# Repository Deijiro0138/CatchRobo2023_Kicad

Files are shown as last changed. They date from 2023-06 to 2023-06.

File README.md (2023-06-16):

# キャチロボ専用基板　仕様書
## マイコン
- Raspberry Pi Pico W x1

## 使用するアクチュエータ・センサ
- ステッピングモーター x2
- サーボ x3
- フォトリフレクタ x4
- 圧電スピーカー x1

## ピン配置
- GP0~2(サーボ)
- GP3(圧電スピーカー)
- GP6(モータ①Step),GP7(モータ①Dir)
- GP10(モータ②Step),GP11(モータ②Dir)
- GP12(遠隔非常停止)
- GP14(アナログマルチプレクサA),GP15(アナログマルチプレクサB)
- GP18~21(DIPスイッチ0-3)
- GP28(センサ読み取り用:ADC)

Raspberry Pi Picoのピン配置

### MD・ステッピングモーター
使用するMDは[STSPIN220](https://akizukidenshi.com/catalog/g/gK-14790/)であり,
**Dirピン→方向**
**Stepピン→回転**
を指定する.

[17HS16-2004S1データシート](https://www.omc-stepperonline.com/download/17HS16-2004S1.pdf) <br>
[Amazon上でのサイトページ](https://www.amazon.co.jp/Nema-%E3%82%B9%E3%83%86%E3%83%83%E3%83%94%E3%83%B3%E3%82%B0%E3%83%A2%E3%83%BC%E3%82%BF-%E3%83%90%E3%82%A4%E3%83%9D%E3%83%BC%E3%83%A91-8%C2%B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)

### アナログマルチプレクサ
アナログマルチプレクサはA,Bの2つの信号で読み取るチャンネルを切り替えられる.以下の真理値表を参照してほしい.
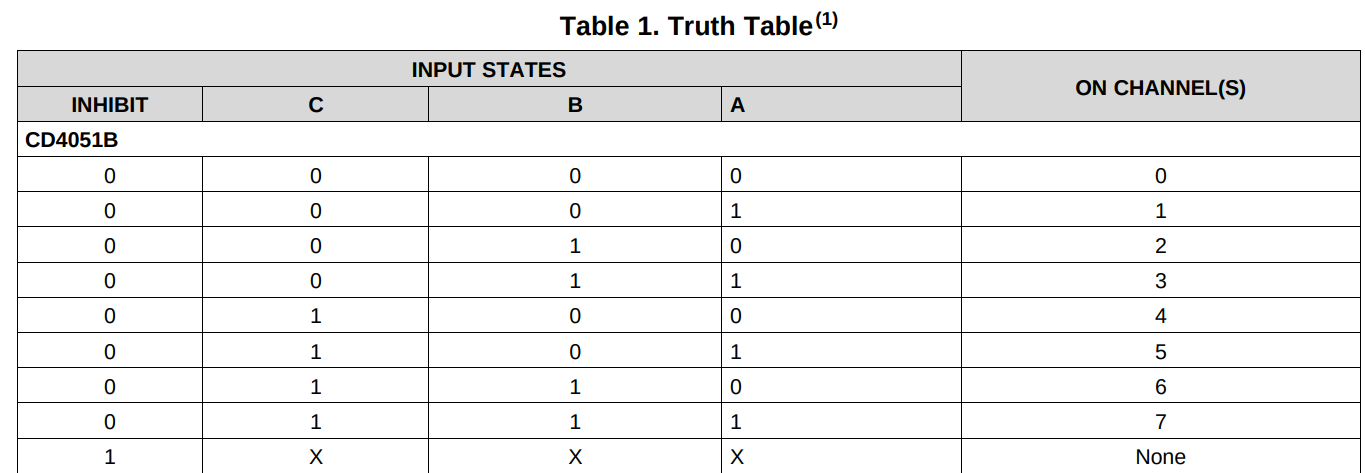
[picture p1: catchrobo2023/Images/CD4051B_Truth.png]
真理値表

AはGP15,BはGP15に接続されている.**GP28のADC機能を用いて,チャンネルを切り替えながら周囲の障害物を検知する.** <br>
[CD4051BM96データシート](https://datasheet.lcsc.com/lcsc/1809261612_Texas-Instruments-CD4051BM96_C21379.pdf)

## 回路図（暫定）
以下のファイルに現在の暫定版の回路図がある.
catchrobo2023/catchrobo2023.pdf
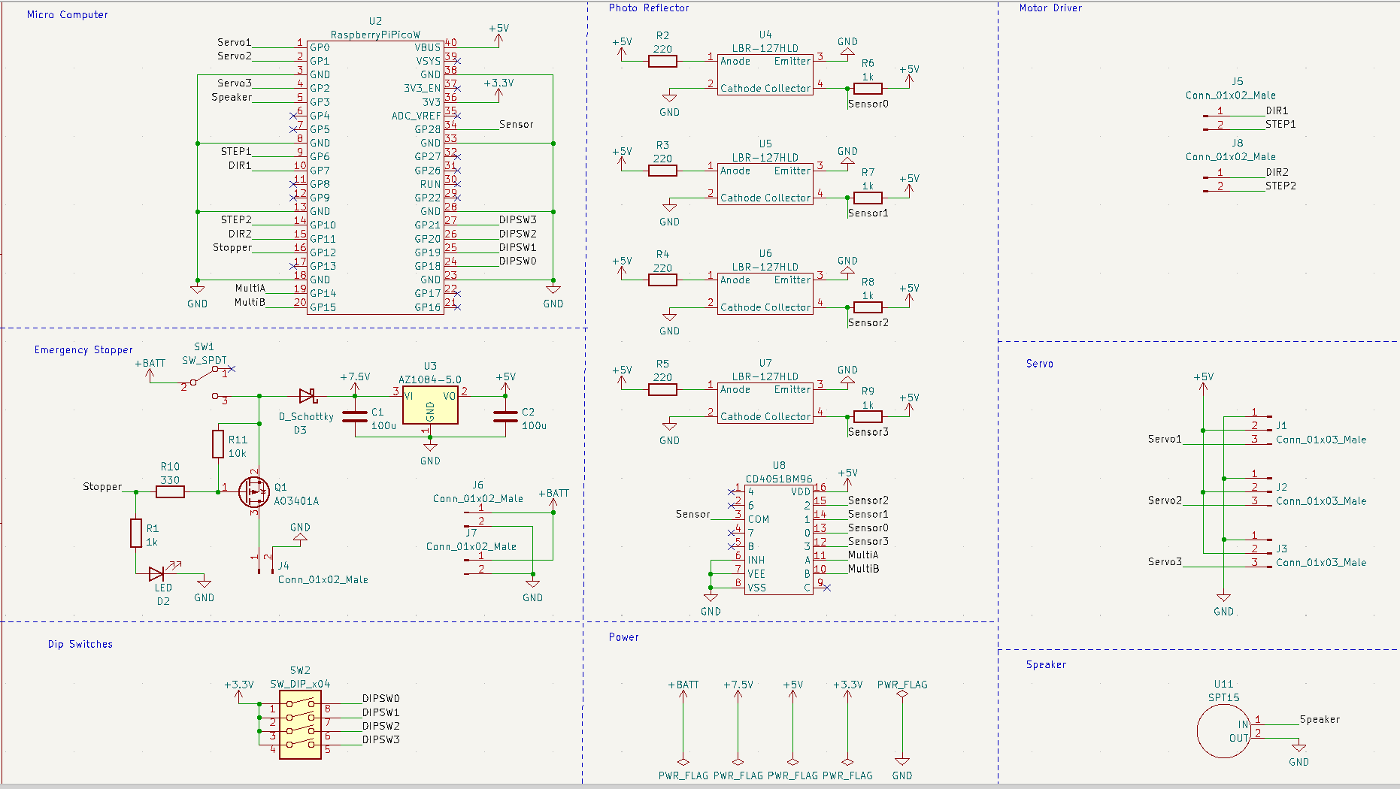
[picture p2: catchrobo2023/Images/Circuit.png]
回路図

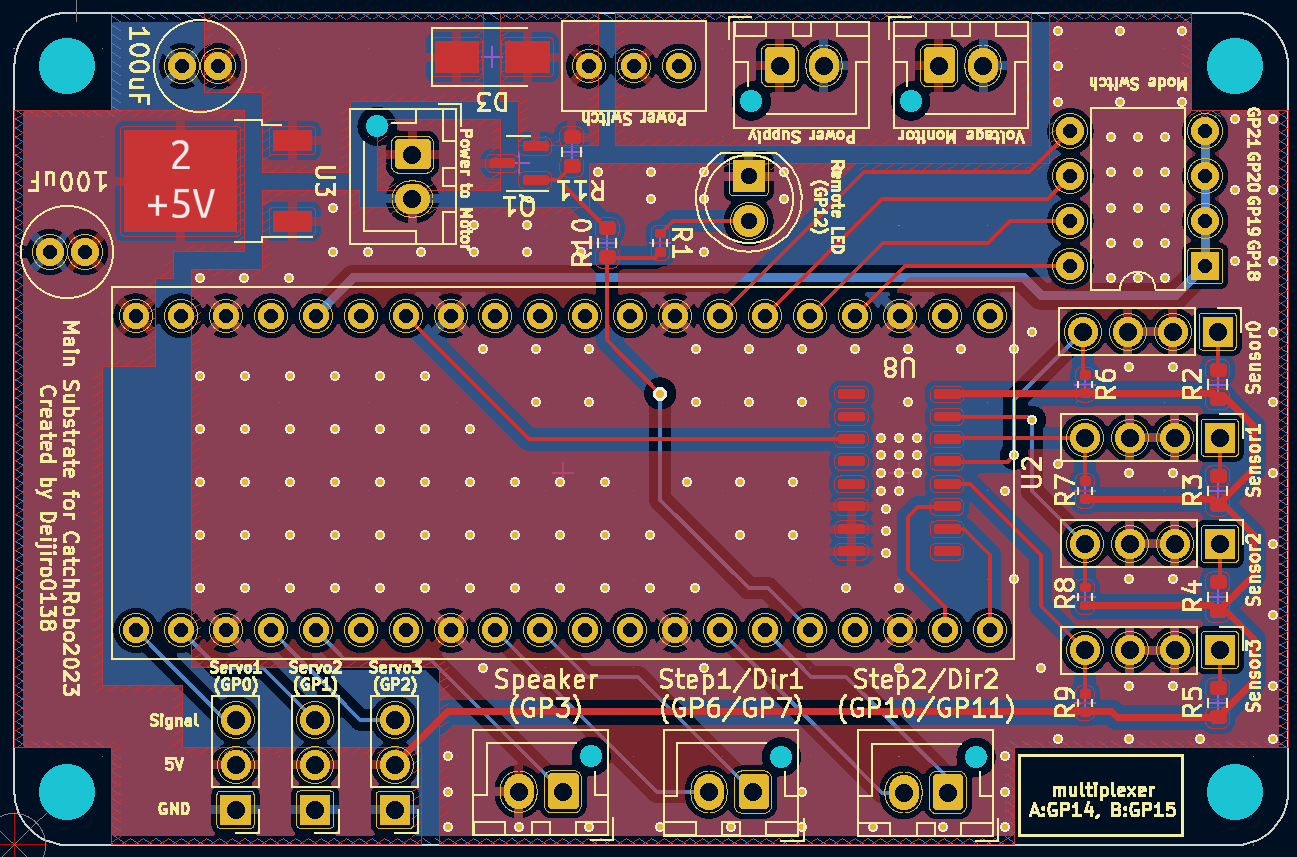
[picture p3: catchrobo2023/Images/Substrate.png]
基板の外形


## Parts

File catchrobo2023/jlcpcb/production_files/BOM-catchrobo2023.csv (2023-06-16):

Comment | Designator | Footprint | LCSC
1k | R1,R6,R7,R8,R9 | R_0402_1005Metric | C11702
AO3401A | Q1 | SOT-23 | C15127
CD4051BM96 | U8 | SOIC-16-150mil | C21379
D_Schottky | D3 | D_SMA | C22452
220 | R2,R3,R4,R5 | R_0603_1608Metric | C22962
330 | R10 | R_0603_1608Metric | C23138
10k | R11 | R_0603_1608Metric | C25804
SPT15 | U11 | JST_XH_B2B-XH-AM_1x02_P2.50mm_Vertical
Conn_01x03_Male | J2 | PinHeader_1x03_P2.54mm_Vertical
100u | C1 | C_Radial_D5.0mm_H11.0mm_P2.00mm
LBR-127HLD | U5 | PinHeader_1x04_P2.54mm_Vertical
LBR-127HLD | U4 | PinHeader_1x04_P2.54mm_Vertical
LBR-127HLD | U7 | PinHeader_1x04_P2.54mm_Vertical
AZ1084-5.0 | U3 | TO-252-2
Conn_01x03_Male | J3 | PinHeader_1x03_P2.54mm_Vertical
Conn_01x02_Male | J5 | JST_XH_B2B-XH-AM_1x02_P2.50mm_Vertical
Conn_01x02_Male | J6 | JST_XH_B2B-XH-AM_1x02_P2.50mm_Vertical
SW_DIP_x04 | SW2 | DIP-8_W7.62mm
Conn_01x02_Male | J4 | JST_XH_B2B-XH-AM_1x02_P2.50mm_Vertical
LED | D2 | LED_D5.0mm
RaspberryPiPicoW | U2 | RaspberryPiPico
Conn_01x02_Male | J8 | JST_XH_B2B-XH-AM_1x02_P2.50mm_Vertical
Conn_01x02_Male | J7 | JST_XH_B2B-XH-AM_1x02_P2.50mm_Vertical
LBR-127HLD | U6 | PinHeader_1x04_P2.54mm_Vertical
SW_SPDT | SW1 | 2MS1-T1-B4-M2-Q-E-S
100u | C2 | C_Radial_D5.0mm_H11.0mm_P2.00mm
Conn_01x03_Male | J1 | PinHeader_1x03_P2.54mm_Vertical

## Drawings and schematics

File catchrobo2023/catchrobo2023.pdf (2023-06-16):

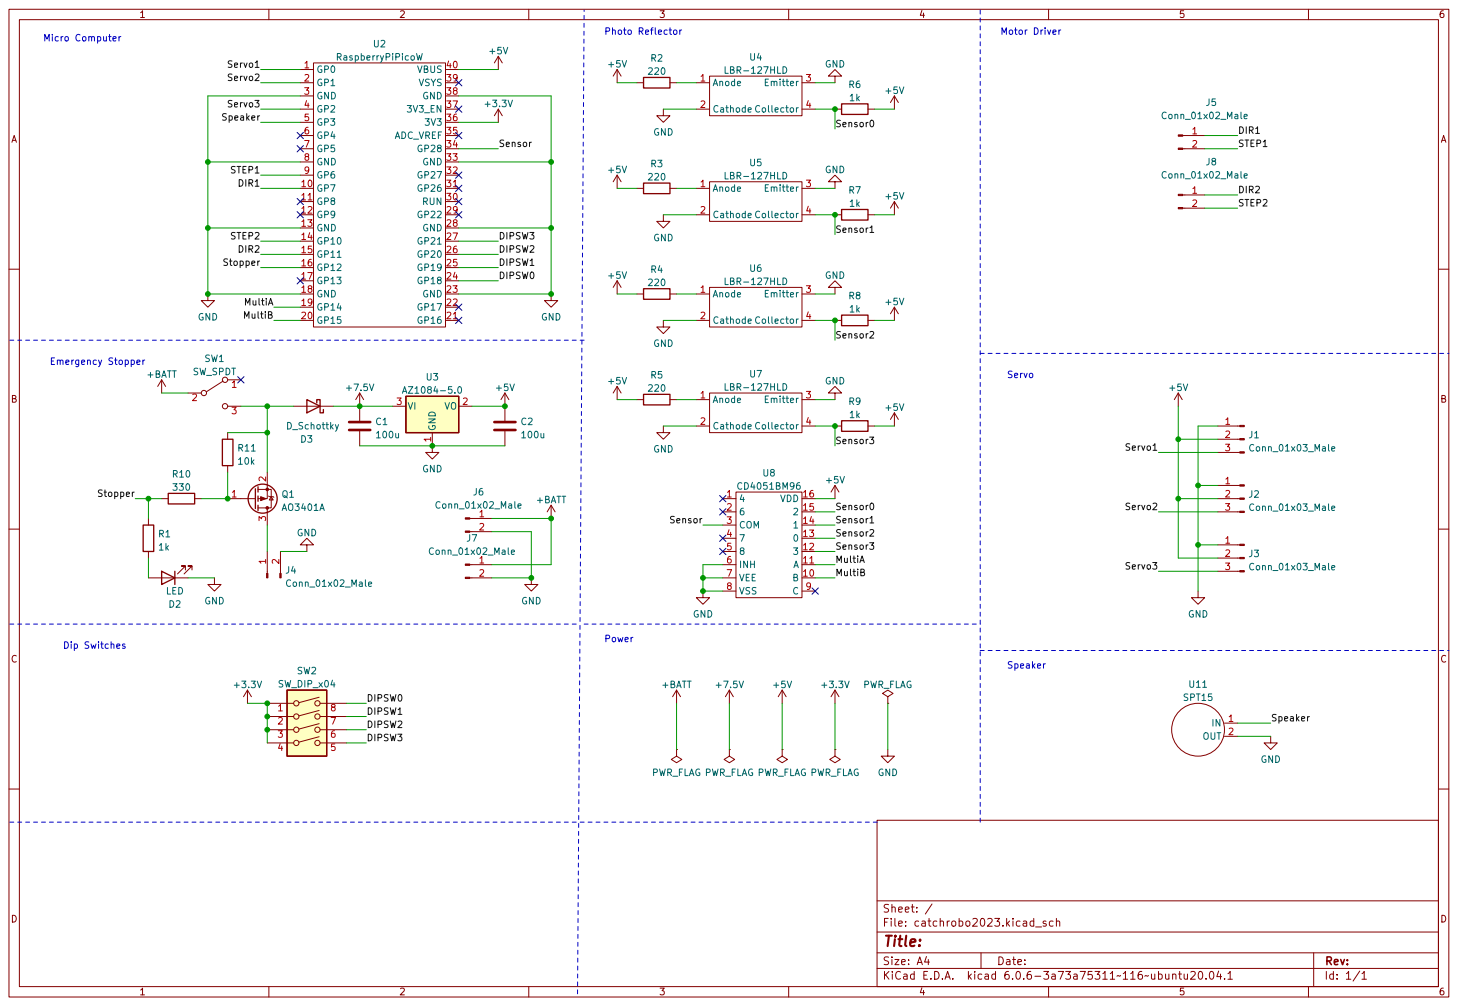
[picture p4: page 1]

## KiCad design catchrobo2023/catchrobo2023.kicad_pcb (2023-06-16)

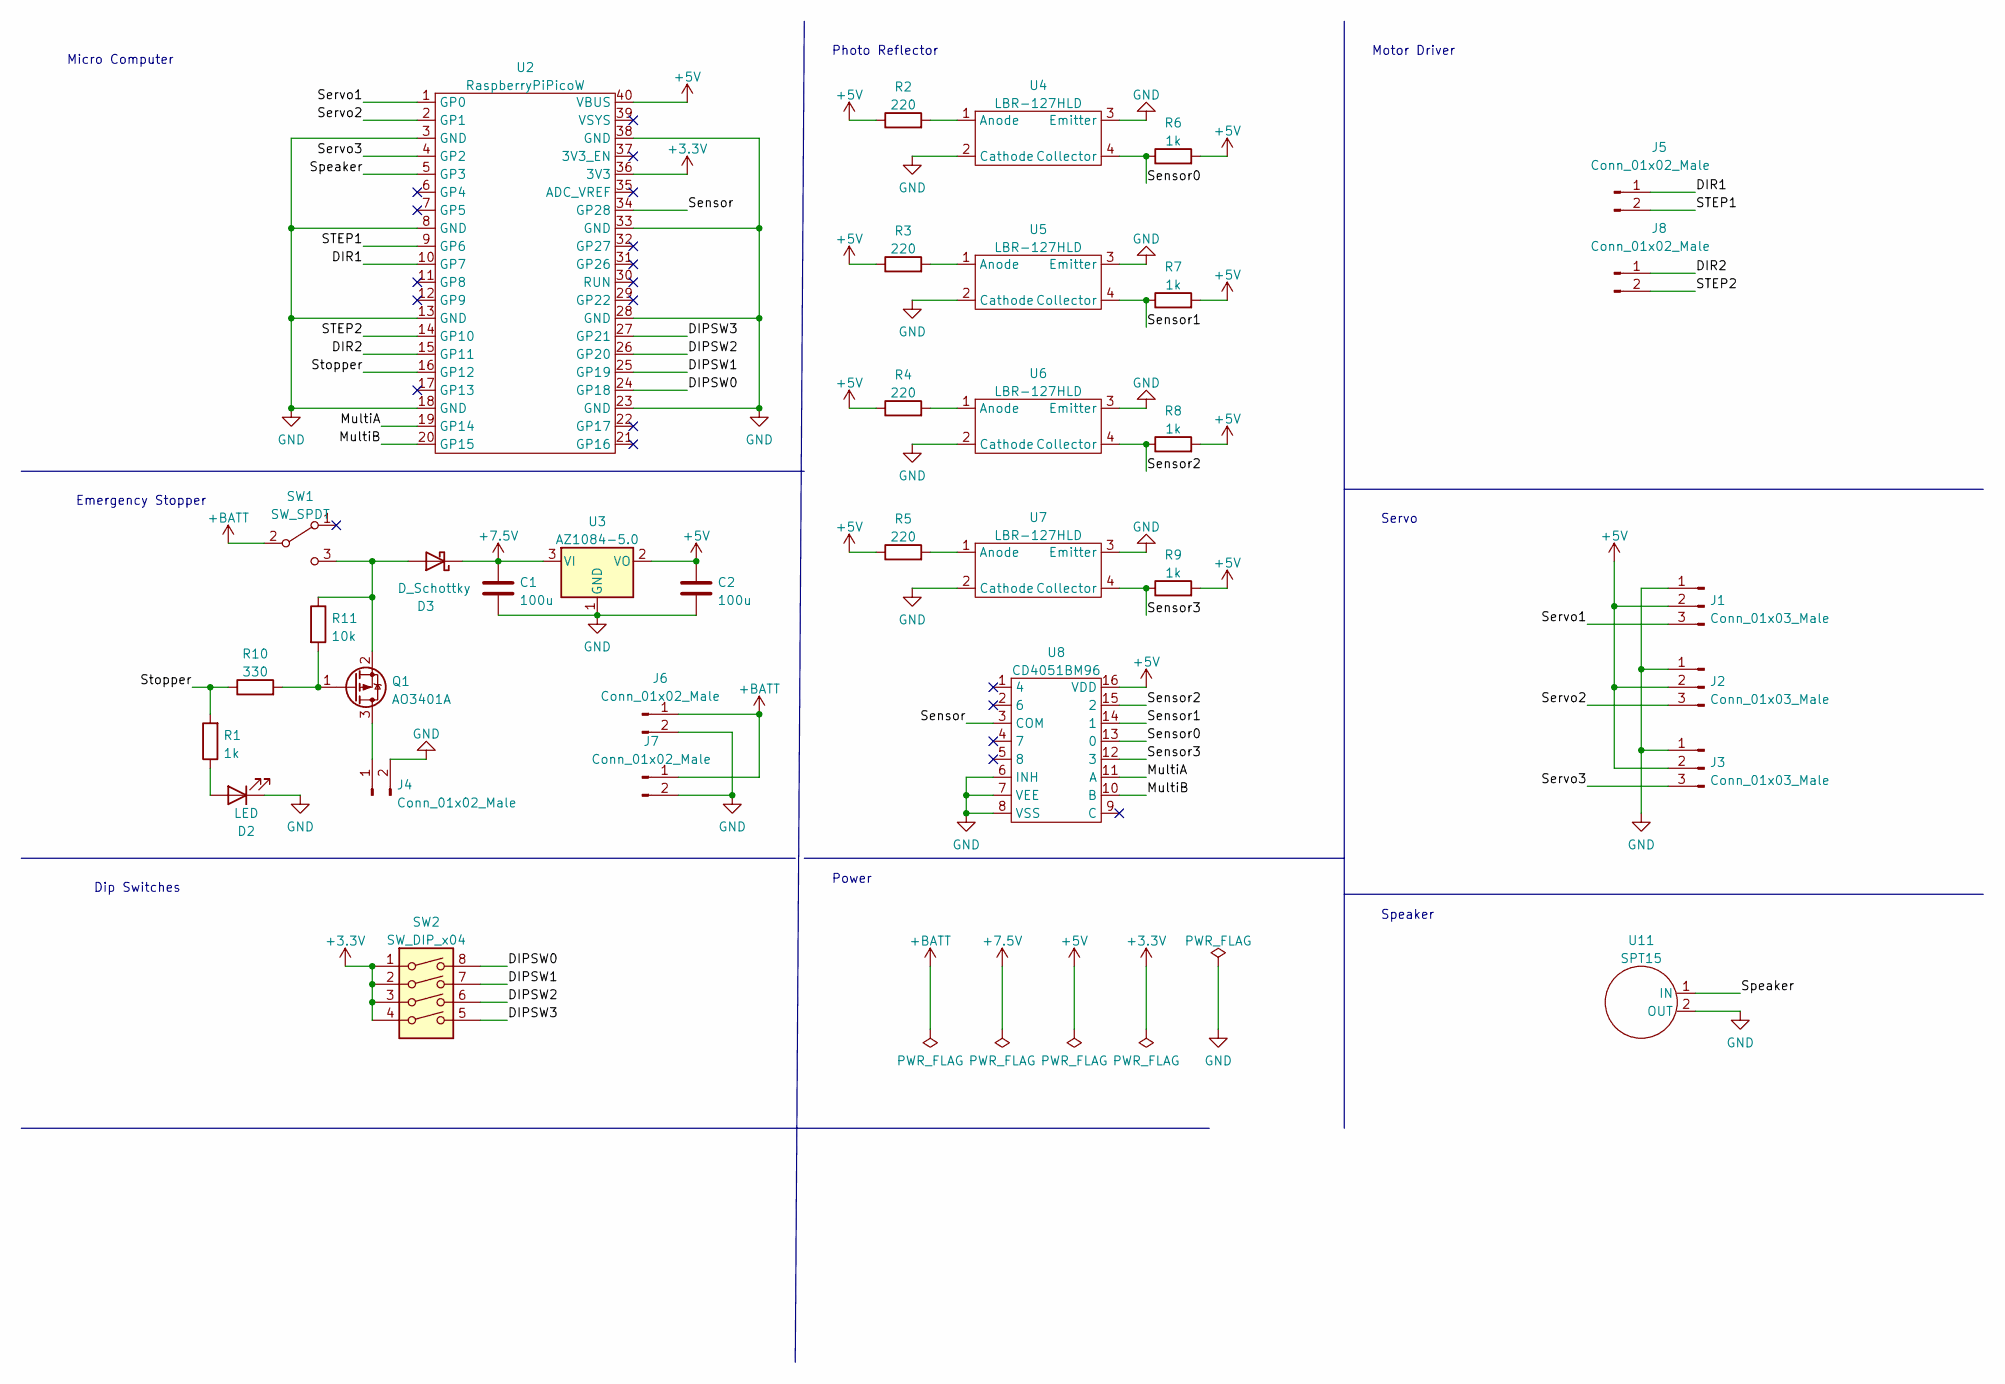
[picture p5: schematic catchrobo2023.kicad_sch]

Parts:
C1, C2: 100u; C_Radial_D5.0mm_H11.0mm_P2.00mm
D2: LED; LED_D5.0mm
D3: D_Schottky; D_SMA; LCSC C22452
J1, J2, J3: Conn_01x03_Male; PinHeader_1x03_P2.54mm_Vertical
J4, J5, J6, J7, J8: Conn_01x02_Male; JST_XH_B2B-XH-AM_1x02_P2.50mm_Vertical
Q1: AO3401A; SOT-23
R1: 1k; R_0402_1005Metric
R2, R3, R4, R5: 220; R_0603_1608Metric; LCSC C22962
R6, R7, R8, R9: 1k; R_0402_1005Metric; LCSC C11702
R10: 330; R_0603_1608Metric; LCSC C23138
R11: 10k; R_0603_1608Metric; LCSC C25804
SW1: SW_SPDT; 2MS1-T1-B4-M2-Q-E-S
SW2: SW_DIP_x04; DIP-8_W7.62mm
U2: RaspberryPiPicoW; RaspberryPiPico
U3: AZ1084-5.0; TO-252-2
U4, U5, U6, U7: LBR-127HLD; PinHeader_1x04_P2.54mm_Vertical
U8: CD4051BM96; SOIC-16-150mil; LCSC C21379
U11: SPT15; JST_XH_B2B-XH-AM_1x02_P2.50mm_Vertical

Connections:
+3.3V: SW2.1, SW2.2, SW2.3, SW2.4, U2.36 (3V3)
+5V: C2.1, J1.2, J2.2, J3.2, R2.1, R3.1, R4.1, R5.1, R6.2, R7.2, R8.2, R9.2, U2.40 (VBUS), U3.2 (VO), U8.16 (VDD)
+7.5V: C1.1, D3.1 (K), U3.3 (VI)
+BATT: J6.1, J7.1, SW1.2 (B)
/DIPSW0: SW2.8, U2.24 (GP18)
/DIPSW1: SW2.7, U2.25 (GP19)
/DIPSW2: SW2.6, U2.26 (GP20)
/DIPSW3: SW2.5, U2.27 (GP21)
/DIR1: J5.1, U2.10 (GP7)
/DIR2: J8.1, U2.15 (GP11)
/MultiA: U2.19 (GP14), U8.11 (A)
/MultiB: U2.20 (GP15), U8.10 (B)
/STEP1: J5.2, U2.9 (GP6)
/STEP2: J8.2, U2.14 (GP10)
/Sensor: U2.34 (GP28), U8.3 (COM)
/Sensor0: R6.1, U4.4 (Collector), U8.13 (0)
/Sensor1: R7.1, U5.4 (Collector), U8.14 (1)
/Sensor2: R8.1, U6.4 (Collector), U8.15 (2)
/Sensor3: R9.1, U7.4 (Collector), U8.12 (3)
/Servo1: J1.3, U2.1 (GP0)
/Servo2: J2.3, U2.2 (GP1)
/Servo3: J3.3, U2.4 (GP2)
/Speaker: U2.5 (GP3), U11.1 (IN)
/Stopper: R1.2, R10.1, U2.16 (GP12)
GND: C1.2, C2.2, D2.1 (K), J1.1, J2.1, J3.1, J4.2, J6.2, J7.2, U2.3 (GND), U2.8 (GND), U2.13 (GND), U2.18 (GND), U2.23 (GND), U2.28 (GND), U2.33 (GND), U2.38 (GND), U3.1 (GND), U4.2 (Cathode), U4.3 (Emitter), U5.2 (Cathode), U5.3 (Emitter), U6.2 (Cathode), U6.3 (Emitter), U7.2 (Cathode), U7.3 (Emitter), U8.6 (INH), U8.7 (VEE), U8.8 (VSS), U11.2 (OUT)
unnamed: D2.2 (A), R1.1
unnamed: D3.2 (A), Q1.2 (S), R11.1, SW1.3 (C)
unnamed: J4.1, Q1.3 (D)
unnamed: Q1.1 (G), R10.2, R11.2
unnamed: R2.2, U4.1 (Anode)
unnamed: R3.2, U5.1 (Anode)
unnamed: R4.2, U6.1 (Anode)
unnamed: R5.2, U7.1 (Anode)

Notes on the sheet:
Dip Switches
Emergency Stopper
Photo Reflector
Motor Driver
Servo
Micro Computer
Speaker
Power

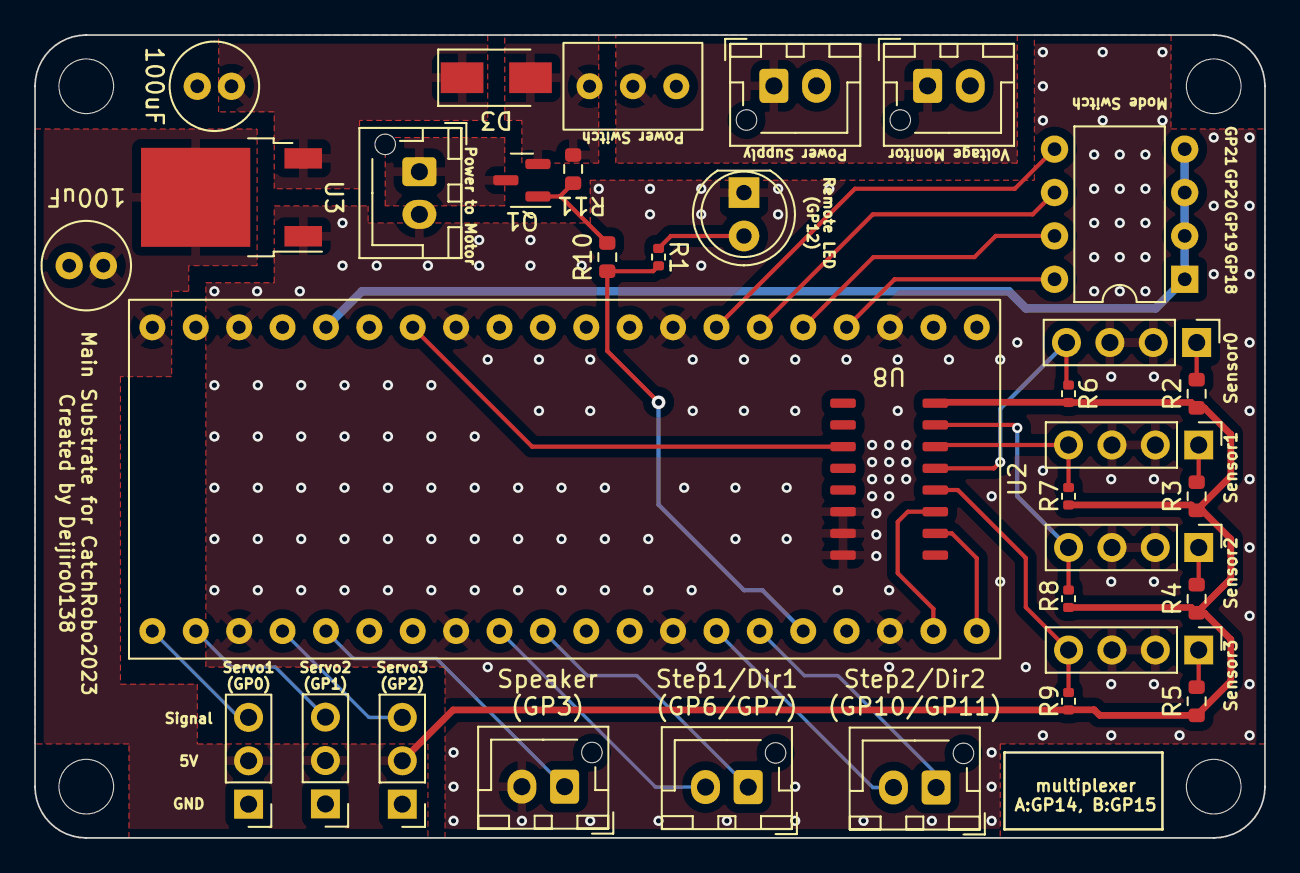
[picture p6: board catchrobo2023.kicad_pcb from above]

Board: 2 copper layers, 72.0 x 47.0 mm, 34 parts (0 on the bottom side), 33 nets.

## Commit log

2023-06-07 サーボ、MD、センサの回路図までは実装
    [catchrobo2023.kicad_sch]
2023-06-07 リレーまで追加
    [catchrobo2023.kicad_sch]
2023-06-11 緊急非常停止以外の回路図は完了
    [catchrobo2023.kicad_sch]
2023-06-13 フットプリントを一部選定
    [catchrobo2023.kicad_sch]
2023-06-13 README追加
    [catchrobo2023.kicad_sch]
2023-06-13 フットプリントの割り当て途中②
    [catchrobo2023.kicad_sch]
2023-06-14 回路図、部品選定が一旦終了
    [catchrobo2023.kicad_sch]
2023-06-14 遠隔非常停止に使用するリレーをFETに変更
    [catchrobo2023.kicad_sch]
2023-06-14 メイン基板作成途中
    [catchrobo2023.kicad_pcb, catchrobo2023.kicad_sch]
2023-06-15 部品配置一旦終わり
    [catchrobo2023.kicad_pcb, catchrobo2023.kicad_sch]
2023-06-15 部品配置完了！
    [catchrobo2023.kicad_pcb, catchrobo2023.kicad_sch]
2023-06-16 基板上のシルクを整備（ピン番号の表記など）
    [catchrobo2023.kicad_pcb]
2023-06-16 READMEの更新
    [catchrobo2023.kicad_pcb]
2023-06-16 フォトリフレクタの周辺を修正
    [catchrobo2023.kicad_pcb, catchrobo2023.kicad_sch]
2023-06-16 一旦、発注に必要なファイルも出力
    [BOM-catchrobo2023.csv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]
2023-06-16 README.mdを更新
2023-06-16 README.mdに画像を追加
2023-06-16 READMEと画像を更新
2023-06-16 README更新
2023-06-16 製造ファイルまで出力
    [CPL-catchrobo2023.csv, catchrobo2023-CuBottom.gbr, catchrobo2023-CuTop.gbr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]
2023-06-16 ロゴの追加
    [catchrobo2023-CuBottom.gbr, catchrobo2023-CuTop.gbr, catchrobo2023-EdgeCuts.gbr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]
2023-06-16 READMEに使用する画像を差し替え
